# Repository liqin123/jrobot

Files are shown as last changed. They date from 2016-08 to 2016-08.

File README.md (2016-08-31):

jrobot
A PLEN Robot Derivative designed at China . We love the PLEN2 robot but its expensive. This is our take on a lower cost version of the PLEN2 robot using 9g servo's.

The 3d printed parts are inspired by the PLEN2 parts but were redrawn from scratch to make use of the cheaper 9g servo motors.

Note: This is a work in progress. We are still busy building and testing it. Proceed at own risk :)

Please get start kits [taobao $120](https://item.taobao.com/item.htm?spm=a230r.1.14.28.0Gwvvy&id=531972040644&ns=1&abbucket=7#detail)

qq group: 371582470
app: jrobot

video demo:http://v.youku.com/v_show/id_XMTcwMTE4NjE5Mg==.html?from=y1.7-2

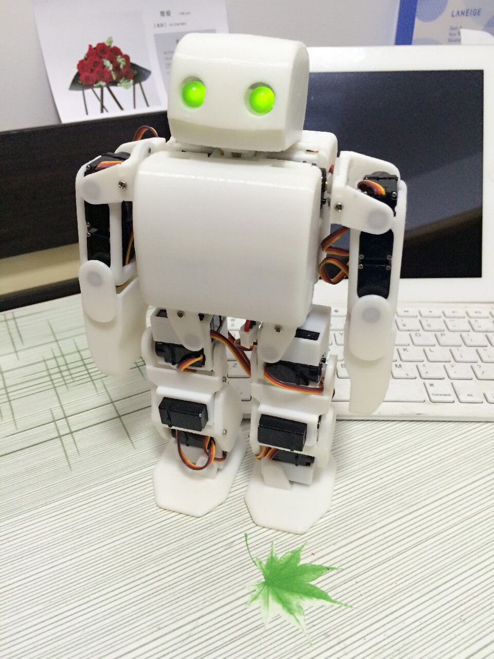
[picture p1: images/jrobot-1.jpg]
3d printed jrobot


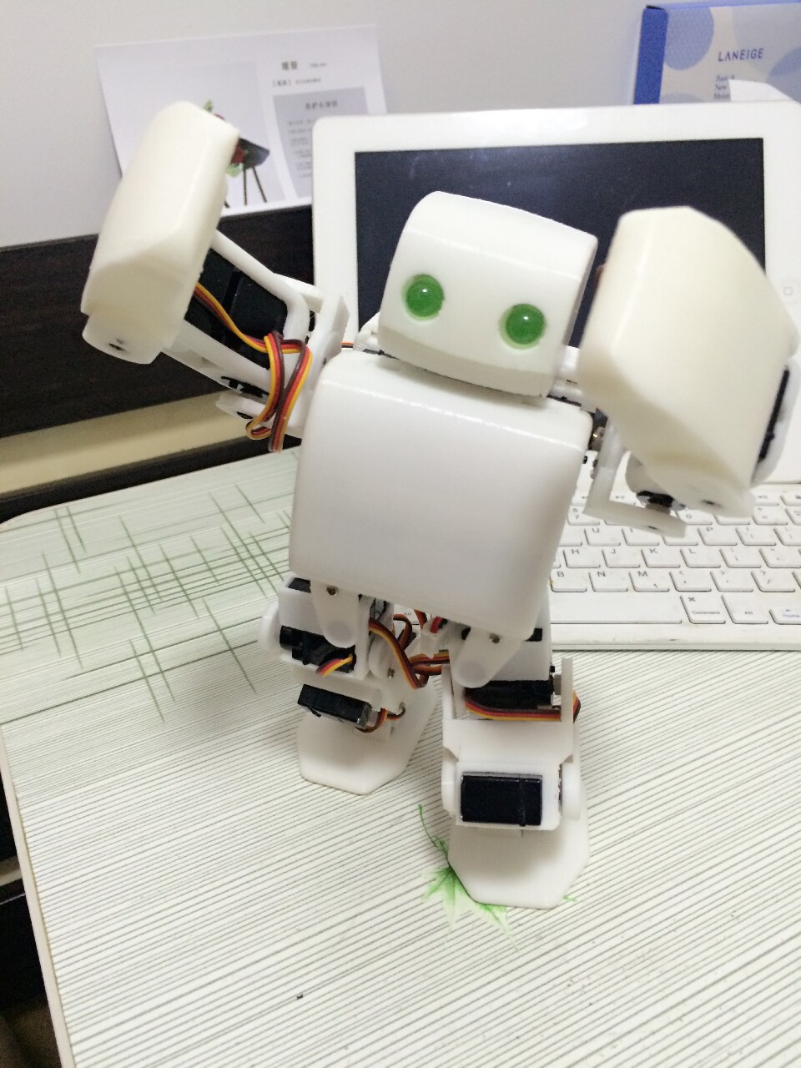
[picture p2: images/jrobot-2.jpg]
3d printed jrobot


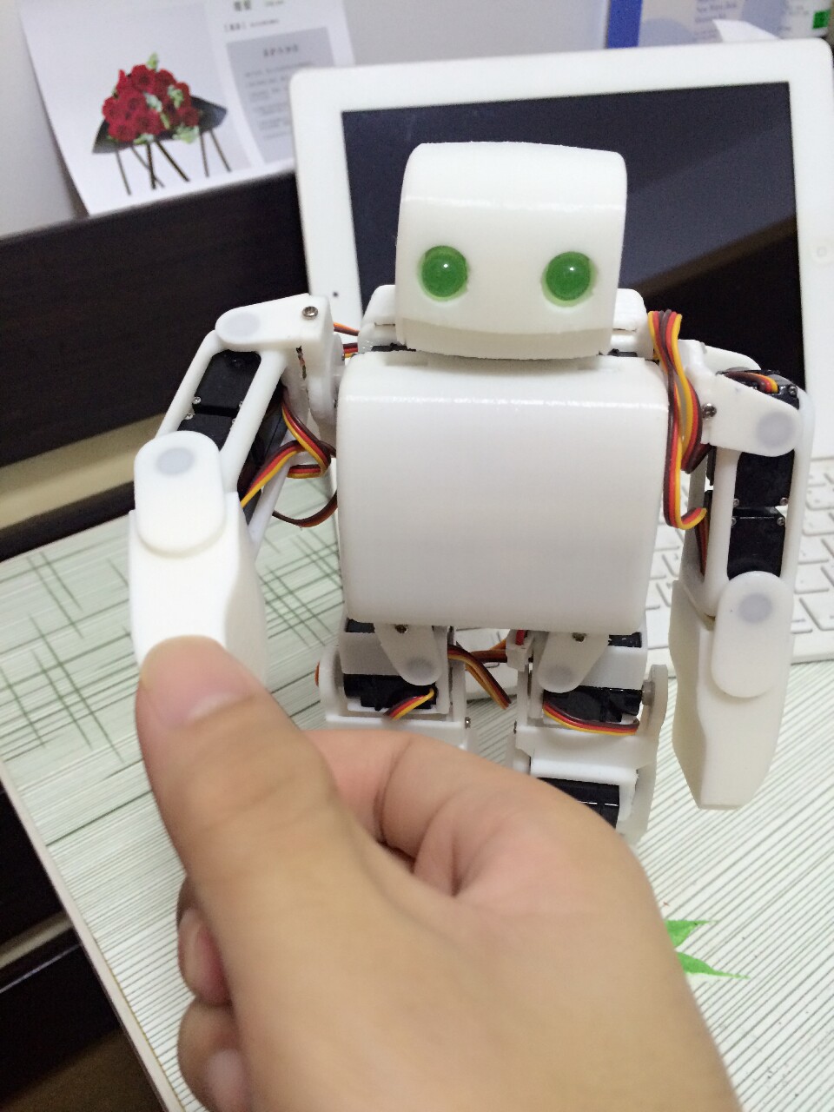
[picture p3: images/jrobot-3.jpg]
3d printed jrobot


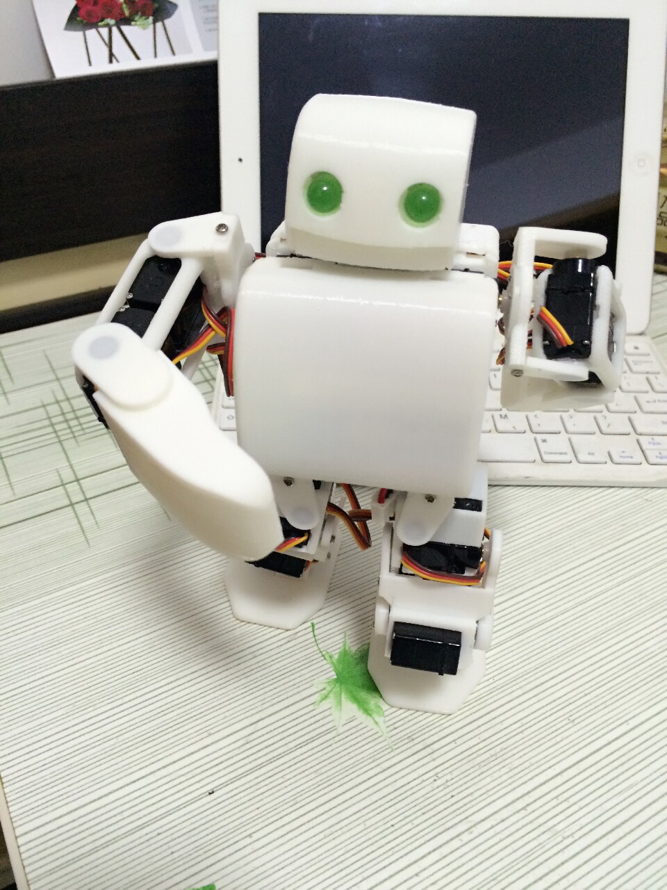
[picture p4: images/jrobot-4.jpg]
3d printed jrobot


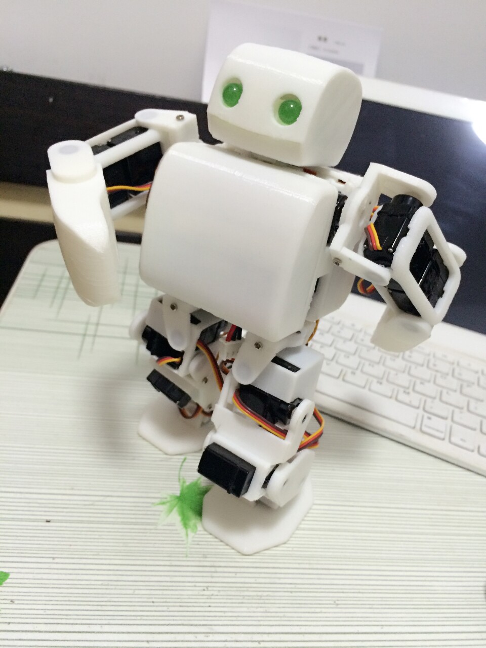
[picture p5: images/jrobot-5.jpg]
3d printed jrobot


This software is released under the MIT License.

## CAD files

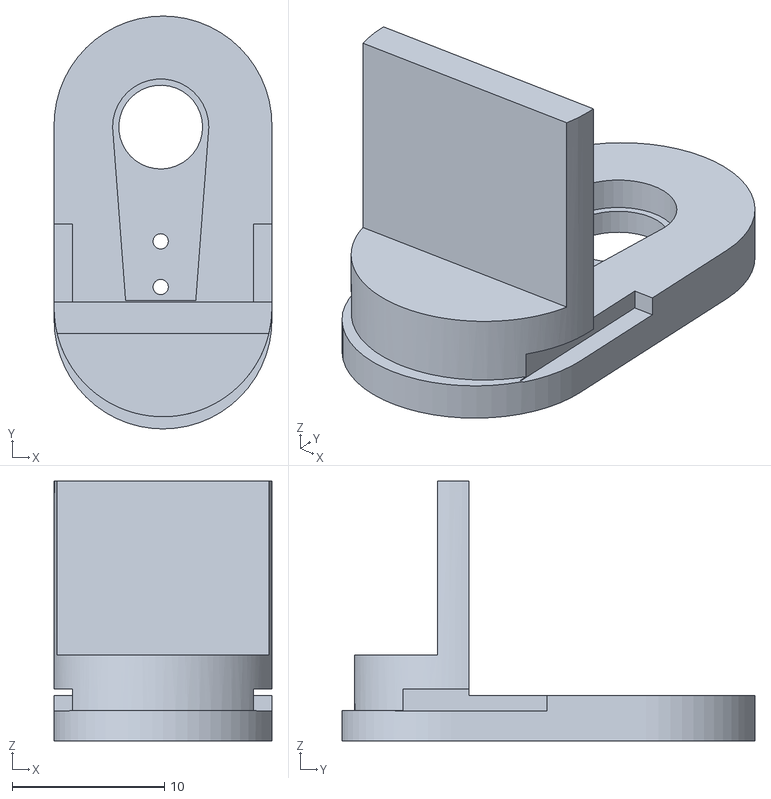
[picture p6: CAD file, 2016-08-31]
stl/servo_bracket_elbow_1.STL
14.3 x 27.1 x 17.1

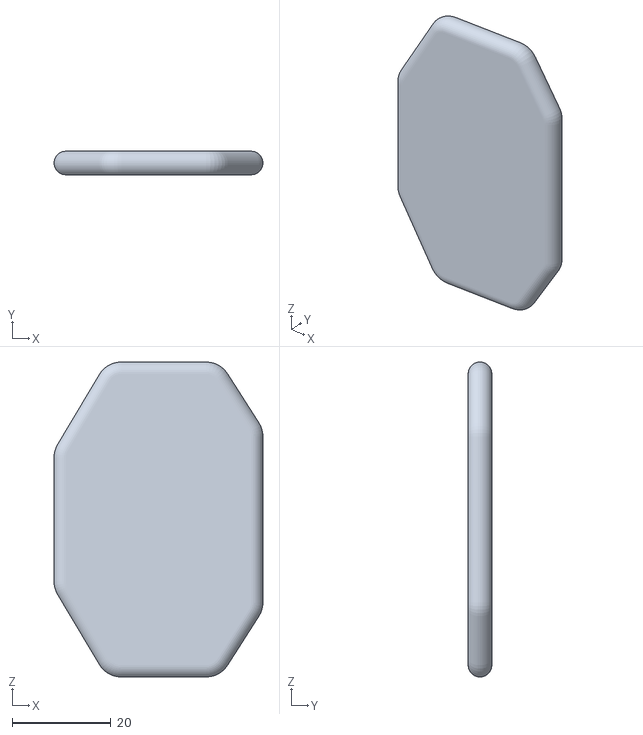
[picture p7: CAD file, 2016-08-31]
stl/foot.STL
42.4 x 4.80 x 63.9

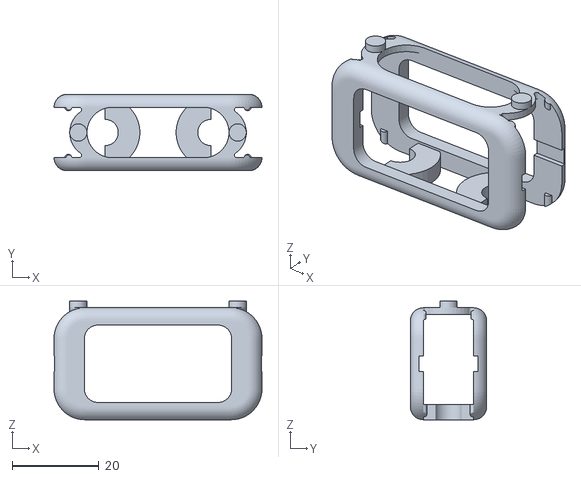
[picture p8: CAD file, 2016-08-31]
stl/servo_assem_type1.STL
47.9 x 17.6 x 27.3

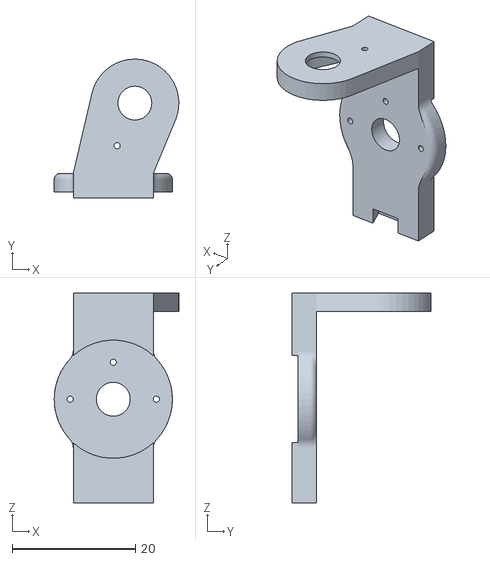
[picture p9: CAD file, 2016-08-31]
stl/servo_type_part2_mirror.STL
20.2 x 22.5 x 34.1

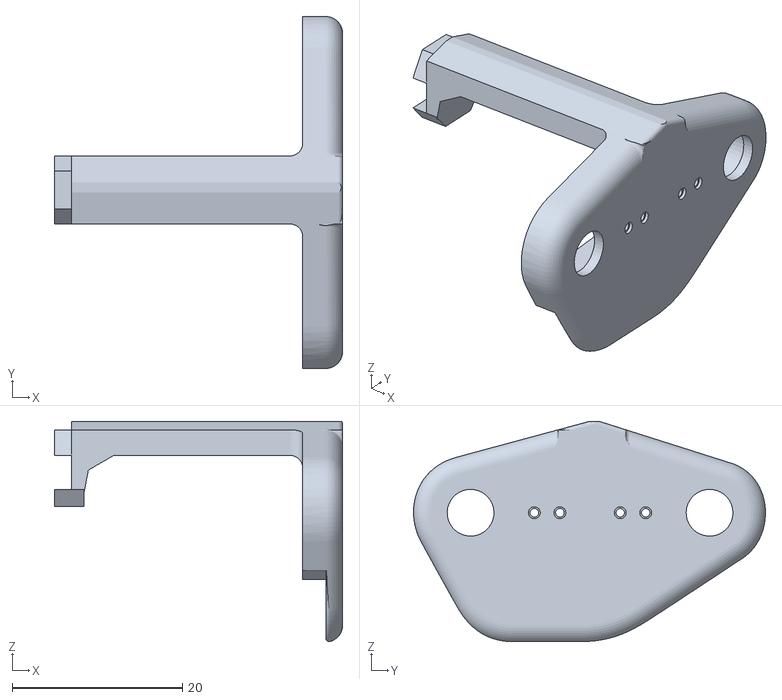
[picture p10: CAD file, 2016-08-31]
stl/servo_bracket_shin_part1.STL
33.9 x 41.4 x 25.9

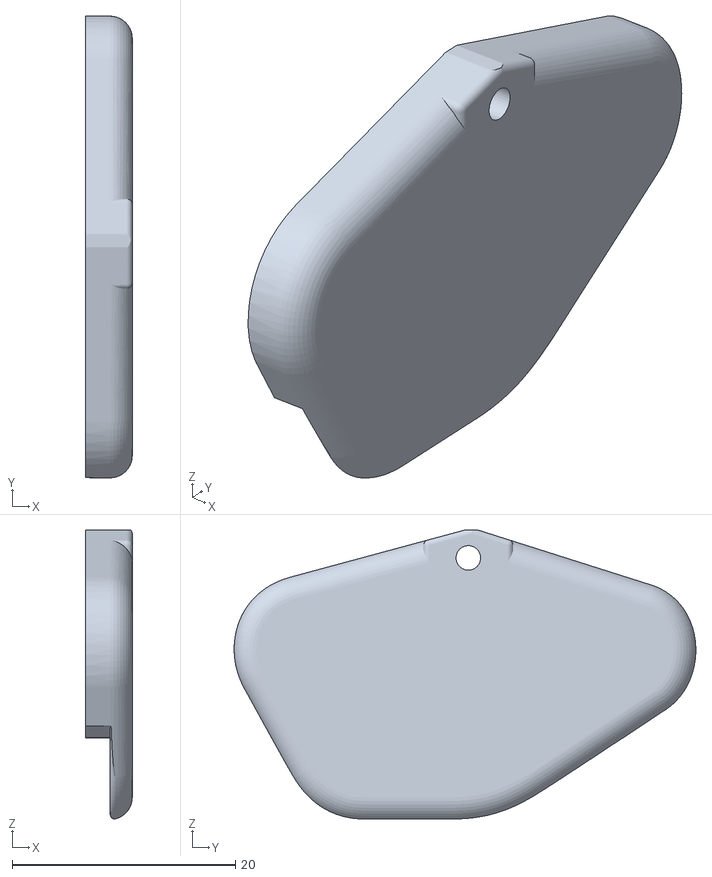
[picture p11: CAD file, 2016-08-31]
stl/servo_bracket_shin_part2.STL
4.18 x 41.4 x 25.9

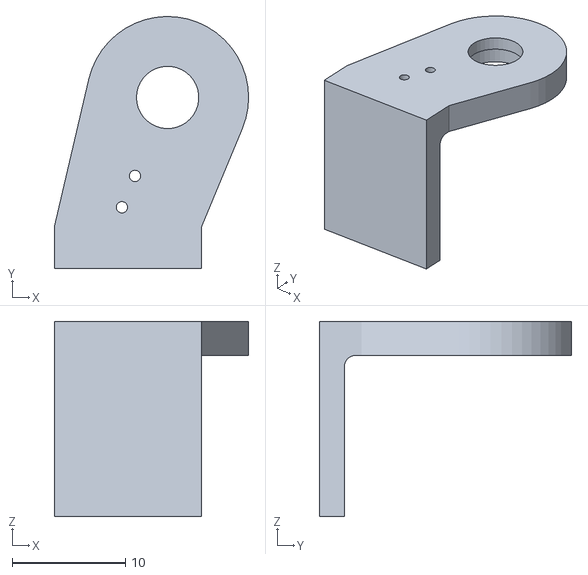
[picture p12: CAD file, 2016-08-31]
stl/servo_bracket_ankle_1_mirror.STL
17.2 x 22.2 x 17.2

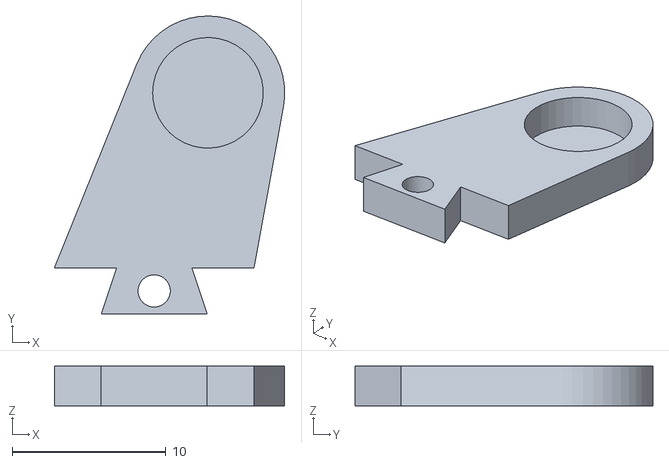
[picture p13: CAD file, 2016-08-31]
stl/servo_type_part1_mirror.STL
15.0 x 19.4 x 2.60

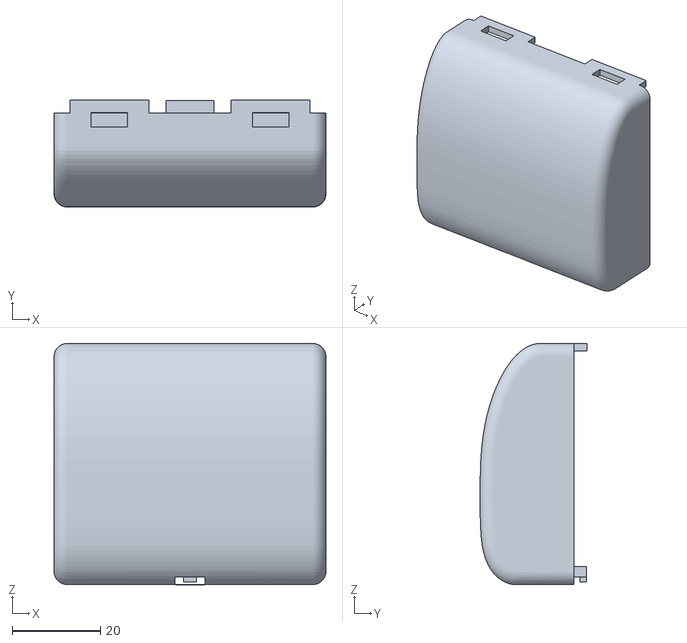
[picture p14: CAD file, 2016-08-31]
stl/body_front.STL
61.6 x 24.2 x 54.6

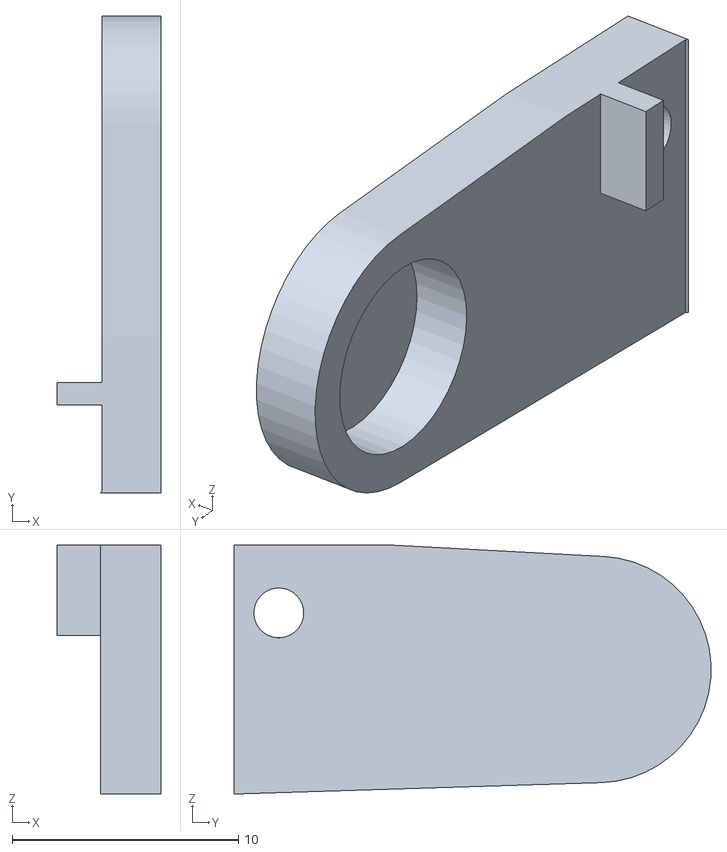
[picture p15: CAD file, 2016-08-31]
stl/servo_bracket_knee_part1_mirror.STL
4.60 x 21.1 x 11.0

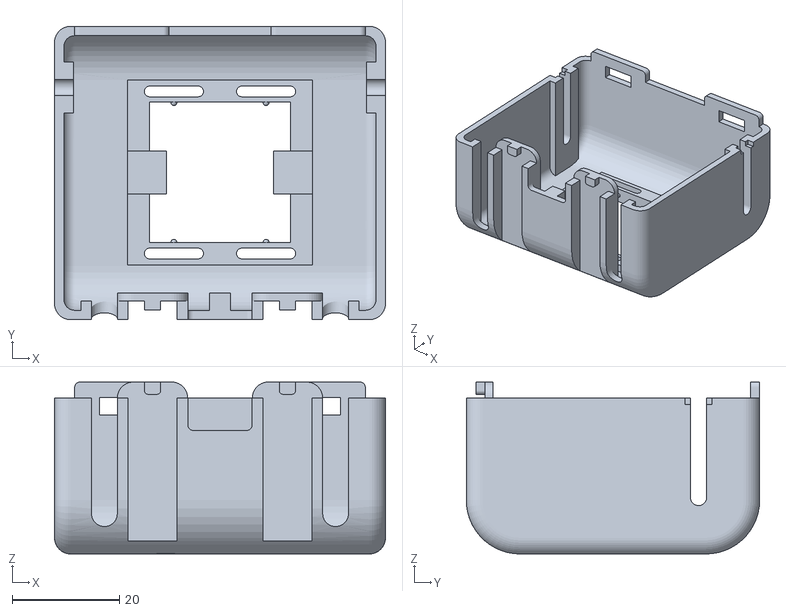
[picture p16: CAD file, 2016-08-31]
stl/body_rear.STL
61.6 x 54.6 x 32.0

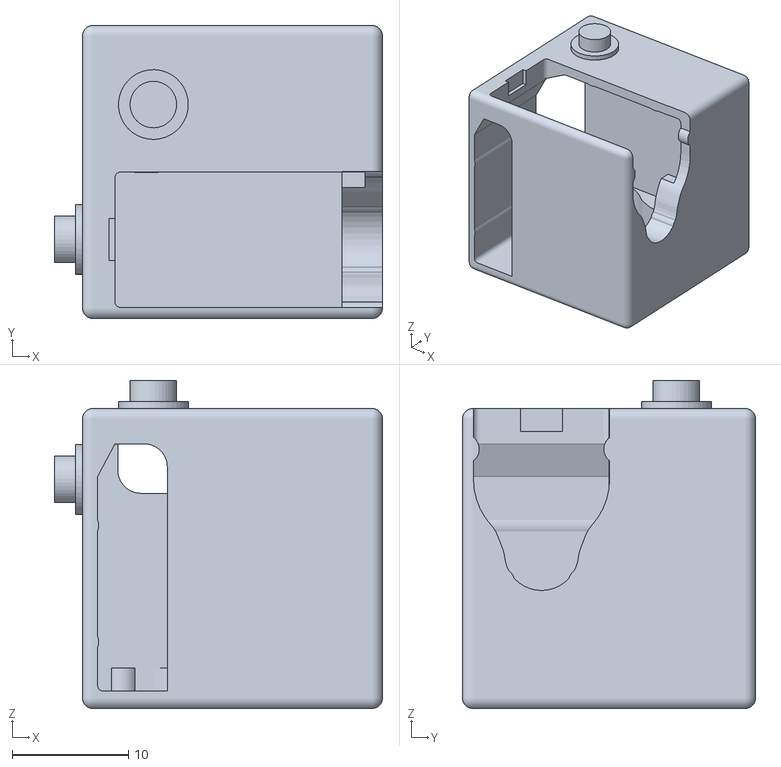
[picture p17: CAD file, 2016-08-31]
stl/servo_assem_type2_mirror.STL
28.2 x 25.2 x 28.2

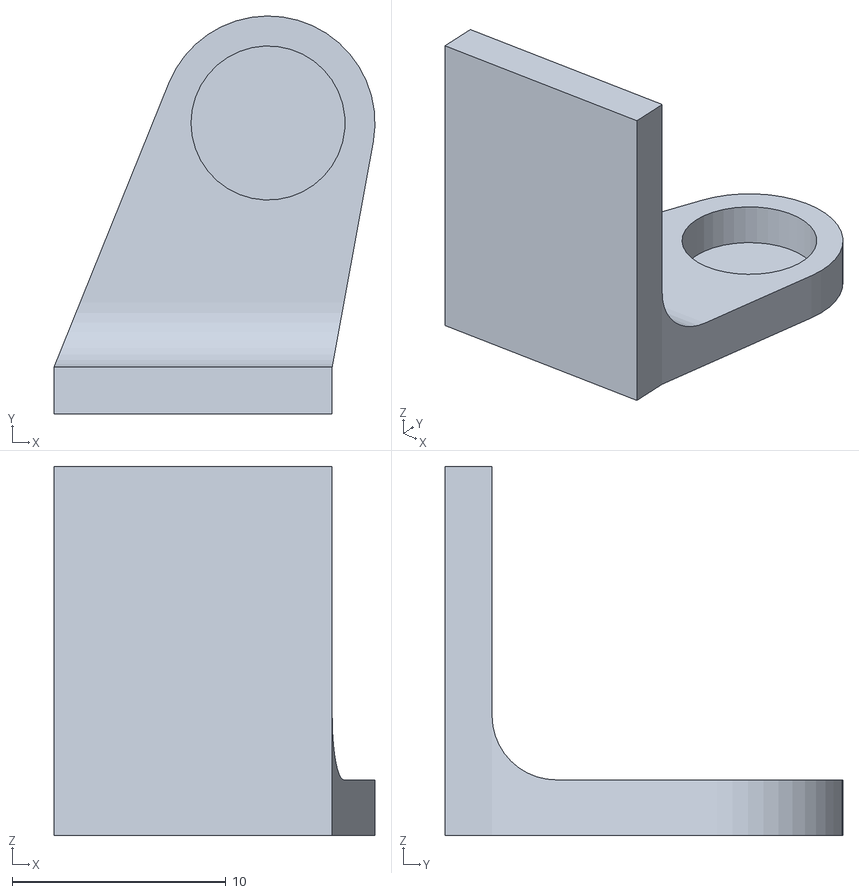
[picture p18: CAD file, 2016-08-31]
stl/servo_bracket_ankle_2_mirror.STL
15.0 x 18.6 x 17.2

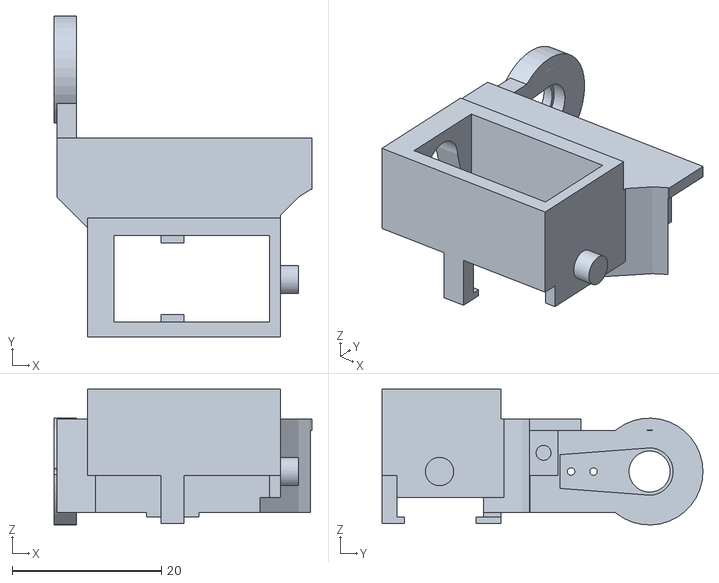
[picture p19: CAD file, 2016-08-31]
stl/servo_bracket_knee_part2_mirror.STL
34.5 x 42.9 x 18.2

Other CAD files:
stl/servo_type_part2.STL
stl/servo_bracket_ankle_1.STL
stl/servo_bracket_shin_part1_mirror.STL
stl/servo_bracket_shin_part2_mirror.STL
stl/barb.STL
stl/body_middle.STL
stl/foot_mirror.STL
stl/servo_assem_type2.STL
stl/servo_bracket_ankle_2.STL
stl/servo_bracket_elbow_2.STL
stl/servo_bracket_knee_part1.STL
stl/servo_bracket_knee_part2.STL
stl/servo_type_part1.STL

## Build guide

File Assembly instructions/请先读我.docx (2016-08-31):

1. 注意点：
  a) 关于电池：出厂锂电处于不饱和状态(不知道有多少电)，请先给电池充满电(充电器灯的状态会从红色->橙色->绿色，绿色时表示电池已经完全充满)
  b) 关于app：可以在IOS 应用市场或在Android二个应用市场 (应用宝 | 豌豆荚) 搜索jrobot 下载。请阅读app左侧菜单栏的帮助和反馈，了解如何配置网络和连接机器人。
  c) 关于app中的网络配置：请在配置前先关闭Robot电源，然后再SSID和密码端填入家里使用的路由器的SSID和密码(务必确保这两项正确，否则配置会失败)，然后打开Robot电源，此时要立刻点击APP中的配置按钮(超过30秒后，Robot会退出接受网络配置状态，进入创建自主热点模式，适合在无网络的地方使用)。若Robot进入了热点模式，可以使用手机在Wifi界面搜索Robot的热点一般名为Jrobot*****的热点，密码为12345678，接着就可以用APP控制Robot了。
  d) 关于舵机回中，PLEN2的仿人形结构和舵机的转动角度范围(<180度)限制每个舵机的初始角度不能是90度，而且每个关节的初始角度不一定一样，切记切记！！！

所以在安装关节的时候，请务必如下操作：

1.关闭主板电源

2.先把舵机插到主板上对应这个关节的舵机插槽

3.打开主板电源，舵机自动转到对应关节的初始位置。

4.关闭主板电源，安装关节。

5.打开主板电源，连上APP，在APP中的开发者模式->回中，将对应的关节微调，调正，然后点回中界面左侧的回中将调整后的回中角度保存到Robot

e) 关于舵机摆臂和轴承的处理：

1.轴承用于虚轴处，固定在打印件上，塞进去后，压平即可。

2.舵机摆臂用到了2中，一种是半一字的摆臂，用在腿各个关节和手关节，只 需要将摆臂末端稍微剪短后放入打印件用胶水固定(也可以关节安装完后再用胶水稍微固定下，前者刚性好，难安装，后者好安装，刚性略差);另外一种摆臂是圆形，用在肩关节和大腿根关节，用胶水固定后，重物压着，牢固后即可以安装。

2. 接线图：

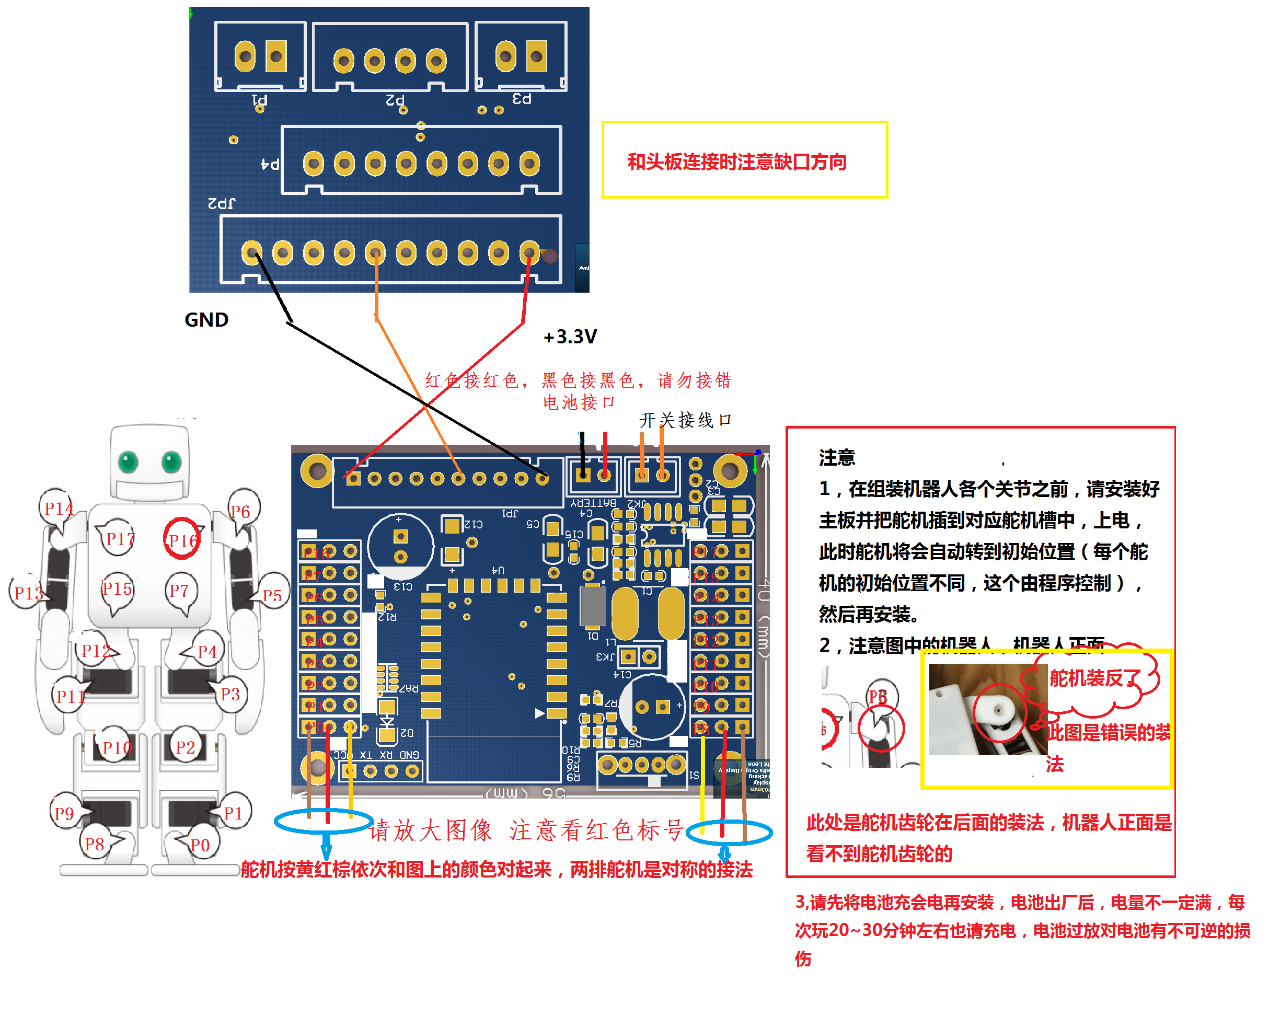
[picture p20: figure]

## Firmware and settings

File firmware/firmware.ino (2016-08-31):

 /*
	Copyright (c) 2015,
	- Kazuyuki TAKASE - https://github.com/junbowu
	- PLEN Project Company Inc. - https://plen.jp

	This software is released under the MIT License.
	(See also : http://opensource.org/licenses/mit-license.php)
*/

#include <string.h>

#include <Wire.h>
#include <Servo.h>

#include "JointController.h"
#include "Motion.h"
#include "MotionController.h"
#include "Interpreter.h"
#include "Pin.h"
#include "Parser.h"
#include "Protocol.h"
#include "System.h"
#include "Profiler.h"
#include "ExternalFs.h"

#if ENSOUL_PLEN2
	#include "AccelerationGyroSensor.h"
	#include "Soul.h"
#endif

namespace
{
	using namespace PLEN2;

	/*!
		Core instances
	*/
	JointController  joint_ctrl;
	MotionController motion_ctrl(joint_ctrl);
	Interpreter      interpreter(motion_ctrl);

	#if ENSOUL_PLEN2
		AccelerationGyroSensor sensor;
		Soul                   soul(sensor, motion_ctrl);
	#endif

	/*!
		The application instance
	*/
	class Application : public Protocol
	{
	private:
		static void (Application::*CONTROLLER_EVENT_HANDLER[])();
		static void (Application::*INTERPRETER_EVENT_HANDLER[])();
		static void (Application::*SETTER_EVENT_HANDLER[])();
		static void (Application::*GETTER_EVENT_HANDLER[])();

		static void (Application::**EVENT_HANDLER[])();

		Motion::Header    m_header_tmp;
		Motion::Frame     m_frame_tmp;
		Interpreter::Code m_code_tmp;

		void applyDiff()
		{
			#if DEBUG_LESS
				volatile Utility::Profiler p(F("Application::applyDiff()"));

				System::debugSerial().print(F(">>> joint_id : "));
				System::debugSerial().println(Utility::hexbytes2uint(m_buffer.data, 2));

				System::debugSerial().print(F(">>> angle_diff : "));
				System::debugSerial().println(Utility::hexbytes2int(m_buffer.data + 2, 3));
			#endif

			joint_ctrl.setAngleDiff(
				Utility::hexbytes2uint(m_buffer.data, 2),
				Utility::hexbytes2int(m_buffer.data + 2, 3)
			);
		}

		void apply()
		{
			#if DEBUG_LESS
				volatile Utility::Profiler p(F("Application::apply()"));
            
				System::debugSerial().print(F(">>> joint_id : "));
				System::debugSerial().println(Utility::hexbytes2uint(m_buffer.data, 2));

				System::debugSerial().print(F(">>> angle : "));
				System::debugSerial().println(Utility::hexbytes2int(m_buffer.data + 2, 3));
			#endif

			joint_ctrl.setAngle(
				Utility::hexbytes2uint(m_buffer.data, 2),
				Utility::hexbytes2int(m_buffer.data + 2, 3)
			);
		}

		void homePosition()
		{
			#if DEBUG_LESS
				volatile Utility::Profiler p(F("Application::homePosition()"));
			#endif

			joint_ctrl.loadSettings();
		}

		void playMotion()
		{
			#if DEBUG_LESS
				volatile Utility::Profiler p(F("Application::playMotion()"));

				System::debugSerial().print(F(">>> slot : "));
				System::debugSerial().println(Utility::hexbytes2uint(m_buffer.data, 2));
			#endif

			motion_ctrl.play(
				Utility::hexbytes2uint(m_buffer.data, 2)
			);
		}

		void stopMotion()
		{
			#if DEBUG_LESS
				volatile Utility::Profiler p(F("Application::stopMotion()"));
			#endif

			motion_ctrl.willStop();
		}

		void popCode()
		{
			#if DEBUG_LESS
				volatile Utility::Profiler p(F("Application::popCode()"));
			#endif

			interpreter.popCode();
		}

		void pushCode()
		{
			#if DEBUG_LESS
				volatile Utility::Profiler p(F("Application::pushCode()"));

				System::debugSerial().print(F(">>> slot : "));
				System::debugSerial().println(Utility::hexbytes2uint(m_buffer.data, 2));

				System::debugSerial().print(F(">>> loop_count : "));
				System::debugSerial().println(Utility::hexbytes2uint(m_buffer.data + 2, 2));
			#endif

			m_code_tmp.slot       = Utility::hexbytes2uint(m_buffer.data, 2);
			m_code_tmp.loop_count = Utility::hexbytes2uint(m_buffer.data + 2, 2) - 1;

			interpreter.pushCode(m_code_tmp);
		}

		void resetInterpreter()
		{
			#if DEBUG_LESS
				volatile Utility::Profiler p(F("Application::resetInterpreter()"));
			#endif

			interpreter.reset();
		}

		void setHome()
		{
			#if DEBUG_LESS
				volatile Utility::Profiler p(F("Application::setHome()"));

				System::debugSerial().print(F(">>> joint_id : "));
				System::debugSerial().println(Utility::hexbytes2uint(m_buffer.data, 2));

				System::debugSerial().print(F(">>> angle : "));
				System::debugSerial().println(Utility::hexbytes2int(m_buffer.data + 2, 3));
			#endif

			joint_ctrl.setHomeAngle(
				Utility::hexbytes2uint(m_buffer.data, 2),
				Utility::hexbytes2int(m_buffer.data + 2, 3)
			);
		}

		void setJointSettings()
		{
			#if DEBUG_LESS
				volatile Utility::Profiler p(F("Application::setJointSettings()"));
			#endif

			joint_ctrl.resetSettings();
		}

		void setMax()
		{
			#if DEBUG_LESS
				volatile Utility::Profiler p(F("Application::setMax()"));

				System::debugSerial().print(F(">>> joint_id : "));
				System::debugSerial().println(Utility::hexbytes2uint(m_buffer.data, 2));

				System::debugSerial().print(F(">>> angle : "));
				System::debugSerial().println(Utility::hexbytes2int(m_buffer.data + 2, 3));
			#endif

			joint_ctrl.setMaxAngle(
				Utility::hexbytes2uint(m_buffer.data, 2),
				Utility::hexbytes2int(m_buffer.data + 2, 3)
			);
		}

		void setMotionFrame()
		{
			#if DEBUG_LESS
				volatile Utility::Profiler p(F("Application::setMotionFrame()"));

				System::debugSerial().print(F(">>> slot : "));
				System::debugSerial().println(Utility::hexbytes2uint(m_buffer.data, 2));

				System::debugSerial().print(F(">>> frame_id : "));
				System::debugSerial().println(Utility::hexbytes2uint(m_buffer.data + 2, 2));

				System::debugSerial().print(F(">>> transition_time_ms : "));
				System::debugSerial().println(Utility::hexbytes2uint(m_buffer.data + 4, 4));

				for (int device_id = 0; device_id < JointController::SUM; device_id++)
				{
					System::debugSerial().print(F(">>> output["));
					System::debugSerial().print(device_id);
					System::debugSerial().print(F("] : "));
					System::debugSerial().println(Utility::hexbytes2int(m_buffer.data + 8 + device_id * 4, 4));
				}
			#endif

			m_frame_tmp.transition_time_ms = Utility::hexbytes2uint(m_buffer.data + 4, 4);

			for (char device_id = 0; device_id < JointController::SUM; device_id++)
			{
				m_frame_tmp.joint_angle[device_id] = Utility::hexbytes2int(m_buffer.data + 8 + device_id * 4, 4);
			}

			if (m_installing)
			{
				if (m_frame_tmp.index < m_header_tmp.frame_length)
				{
					m_frame_tmp.set(m_header_tmp.slot);
					m_frame_tmp.index++;
				}

				if (m_frame_tmp.index == m_header_tmp.frame_length)
				{
					m_installing = false;
				}
				else
				{
					readByte('>');
					accept();
					transitState();

					readByte('m');
					readByte('f');
					accept();
					transitState();

					readByte('0'); // dummy
					readByte('0'); // dummy
					readByte('0'); // dummy
					readByte('0'); // dummy
				}
			}
			else
			{
				m_frame_tmp.index = Utility::hexbytes2uint(m_buffer.data + 2, 2);
				m_frame_tmp.set(Utility::hexbytes2uint(m_buffer.data, 2));
			}
		}

		void setMotionHeader()
		{
			strncpy(m_header_tmp.name, m_buffer.data + 2, 20);
			m_header_tmp.name[20] = '\0';
			m_buffer.data[2]      = '\0';

			if (   !(m_parser[ARGUMENTS_INCOMING]->parse(m_buffer.data))
				|| !(m_parser[ARGUMENTS_INCOMING]->parse(m_buffer.data + 22)) )
			{
				return;
			}

			#if DEBUG_LESS
				volatile Utility::Profiler p(F("Application::setMotionHeader()"));

				System::debugSerial().print(F(">>> slot : "));
				System::debugSerial().println(Utility::hexbytes2uint(m_buffer.data, 2));

				System::debugSerial().print(F(">>> name : "));
				System::debugSerial().println(m_header_tmp.name);

				System::debugSerial().print(F(">>> func : "));
				System::debugSerial().println(Utility::hexbytes2uint(m_buffer.data + 22, 2));

				System::debugSerial().print(F(">>> arg0 : "));
				System::debugSerial().println(Utility::hexbytes2uint(m_buffer.data + 24, 2));

				System::debugSerial().print(F(">>> arg1 : "));
				System::debugSerial().println(Utility::hexbytes2uint(m_buffer.data + 26, 2));

				System::debugSerial().print(F(">>> frame_length : "));
				System::debugSerial().println(Utility::hexbytes2uint(m_buffer.data + 28, 2));
			#endif

			m_header_tmp.slot         = Utility::hexbytes2uint(m_buffer.data, 2);
			m_header_tmp.frame_length = Utility::hexbytes2uint(m_buffer.data + 28, 2);

			switch (Utility::hexbytes2uint(m_buffer.data + 22, 2))
			{
				case 0:
				{
					m_header_tmp.use_loop = 0;
					m_header_tmp.use_jump = 0;

					break;
				}

				case 1:
				{
					m_header_tmp.use_loop   = 1;
					m_header_tmp.use_jump   = 0;
					m_header_tmp.loop_begin = Utility::hexbytes2uint(m_buffer.data + 24, 2);
					m_header_tmp.loop_end   = Utility::hexbytes2uint(m_buffer.data + 26, 2);

					break;
				}

				case 2:
				{
					m_header_tmp.use_loop  = 0;
					m_header_tmp.use_jump  = 1;
					m_header_tmp.jump_slot = Utility::hexbytes2uint(m_buffer.data + 24, 2);

					break;
				}
			}

			m_header_tmp.set();

			if (m_installing == true)
			{
				readByte('>');
				accept();
				transitState();

				readByte('m');
				readByte('f');
				accept();
				transitState();

				readByte('0'); // dummy
				readByte('0'); // dummy
				readByte('0'); // dummy
				readByte('0'); // dummy

				m_frame_tmp.index = 0;
			}
		}

		void setMin()
		{
			#if DEBUG_LESS
				volatile Utility::Profiler p(F("Application::setMin()"));

				System::debugSerial().print(F(">>> joint_id : "));
				System::debugSerial().println(Utility::hexbytes2uint(m_buffer.data, 2));

				System::debugSerial().print(F(">>> angle : "));
				System::debugSerial().println(Utility::hexbytes2int(m_buffer.data + 2, 3));
			#endif

			joint_ctrl.setMinAngle(
				Utility::hexbytes2uint(m_buffer.data, 2),
				Utility::hexbytes2int(m_buffer.data + 2, 3)
			);
		}

		void getJointSettings()
		{
			#if DEBUG_LESS
				volatile Utility::Profiler p(F("Application::getJointSettings()"));
			#endif

			joint_ctrl.dump();
		}

		void getMotion()
		{
			#if DEBUG_LESS
				volatile Utility::Profiler p(F("Application::getMotion()"));

				System::debugSerial().print(F(">>> slot : "));
				System::debugSerial().println(Utility::hexbytes2uint(m_buffer.data, 2));
			#endif

			motion_ctrl.dump(
				Utility::hexbytes2uint(m_buffer.data, 2)
			);
		}

		void getVersionInformation()
		{
			#if DEBUG_LESS
				volatile Utility::Profiler p(F("Application::getVersionInformation()"));
			#endif

			System::dump();
		}

	public:
		virtual void afterHook()
		{
			#if DEBUG
				volatile Utility::Profiler p(F("Application::afterFook()"));
			#endif

			if (m_state == HEADER_INCOMING)
			{
				unsigned char header_id = m_parser[HEADER_INCOMING ]->index();
				unsigned char cmd_id    = m_parser[COMMAND_INCOMING]->index();

				(this->*EVENT_HANDLER[header_id][cmd_id])();

				#if ENSOUL_PLEN2
					soul.userActionInputed();
				#endif
			}
		}
	};

	void (Application::*Application::CONTROLLER_EVENT_HANDLER[])() = {
		&Application::applyDiff,
		&Application::apply,
		&Application::homePosition,
		&Application::playMotion,
		&Application::stopMotion,
		&Application::playMotion,
		&Application::stopMotion
	};

	void (Application::*Application::INTERPRETER_EVENT_HANDLER[])() = {
		&Application::popCode,
		&Application::pushCode,
		&Application::resetInterpreter
	};

	void (Application::*Application::SETTER_EVENT_HANDLER[])() = {
		&Application::setHome,
		&Application::setMotionHeader, // sanity check.
		&Application::setJointSettings,
		&Application::setMax,
		&Application::setMotionFrame,
		&Application::setMotionHeader,
		&Application::setMin
	};

	void (Application::*Application::GETTER_EVENT_HANDLER[])() = {
		&Application::getJointSettings,
		&Application::getMotion,
		&Application::getVersionInformation
	};

	void (Application::**Application::EVENT_HANDLER[])() = {
		Application::CONTROLLER_EVENT_HANDLER,
		Application::INTERPRETER_EVENT_HANDLER,
		Application::SETTER_EVENT_HANDLER,
		Application::GETTER_EVENT_HANDLER
	};

	Application app;
}


/*!
	@brief Setup

	Put your setup code here, to run once:

	@attention
	Digital pin's output is an indefinite if you don't give an initialize value.
	Please ensure that setup the pins which are configurable.
*/
void setup()
{
	volatile PLEN2::System system;
	ExternalFs::init();

	joint_ctrl.Init();
	joint_ctrl.loadSettings();
	System::setup_smartconfig();

	#if ENSOUL_PLEN2
		/*!
			@attention
			The order of power supplied or firmware startup timing is base-board, head-board.
			If the sampling method calls from early timing, program freezes because synchronism of communication is missed.
			(Generally, it is going to success setup() inserts 3000[msec] delays.)
		*/
		delay(3000);
	#endif

	#if DEBUG
		while (!Serial);

		PLEN2::System::outputSerial().println(
			F("Hello, I am PLEN2! My system is up and running ver.1.3.1, Let me walk :)")
		);
	#endif
}


/*!
	@brief Main polling loop

	Put your main code here, to run repeatedly:
*/
void loop()
{
	if (motion_ctrl.playing())
	{
		if (motion_ctrl.frameUpdatable())
		{
			motion_ctrl.updateFrame();
		}

		if (motion_ctrl.updatingFinished())
		{
			if (motion_ctrl.nextFrameLoadable())
			{
				motion_ctrl.loadNextFrame();
			}
			else
			{
				motion_ctrl.stop();

				if (interpreter.ready())
				{
					interpreter.popCode();
				}
			}
		}
	}

	if (PLEN2::System::SystemSerial().available())
	{
		app.readByte(PLEN2::System::SystemSerial().read());

		if (app.accept())
		{
			app.transitState();

		}
	}
	if (PLEN2::System::tcp_available())
	{
	#if DEBUG_LESS
	    uint8_t c = PLEN2::System::tcp_read();
     	    PLEN2::System::outputSerial().write(c);
     	    app.readByte(c);
        #else
            app.readByte(PLEN2::System::tcp_read());
        #endif
	    if (app.accept())
	    {
	        app.transitState();
	    }
	}

	PLEN2::System::handleClient();
	#if ENSOUL_PLEN2
		soul.log();
		soul.action();
	#endif
}

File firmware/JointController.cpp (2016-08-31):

/*
	Copyright (c) 2015,
	- Kazuyuki TAKASE - https://github.com/junbowu
	- PLEN Project Company Inc. - https://plen.jp

	This software is released under the MIT License.
	(See also : http://opensource.org/licenses/mit-license.php)
*/
#include "Arduino.h"
#include <Wire.h>
#include <Servo.h>
#include <Ticker.h>
#include <Adafruit_PWMServoDriver.h>

#include "Pin.h"
#include "Profiler.h"
#include "System.h"
#include "JointController.h"
#include "ExternalFs.h"
#include "Motion.h"

Adafruit_PWMServoDriver pwm;
Servo GPIO12SERVO;
Servo GPIO14SERVO;
Servo EyeOut;
Ticker flipper;
Ticker flipper_second;

extern File fp_config;
/*!
	@note
	If you want to apply the firmware to PLEN1.4, set the macro to false.
*/
#define PLEN2_JOINTCONTROLLER_PWM_OUT_00_07_REGISTER OCR1C
#define PLEN2_JOINTCONTROLLER_PWM_OUT_08_15_REGISTER OCR1B
#define PLEN2_JOINTCONTROLLER_PWM_OUT_16_23_REGISTER OCR1A

volatile bool PLEN2::JointController::m_1cycle_finished = false;
int PLEN2::JointController::m_pwms[PLEN2::JointController::SUM];

//eyes control
int _enable;
int _eye_count_step;
int _eye_count;

namespace
{
	namespace Shared
	{
		using namespace PLEN2;

		PROGMEM const int m_SETTINGS_INITIAL[] =
		{
			JointController::ANGLE_MIN, JointController::ANGLE_MAX,  -40, // [01] Left : Shoulder Pitch
			JointController::ANGLE_MIN, JointController::ANGLE_MAX,  245, // [02] Left : Thigh Yaw
			JointController::ANGLE_MIN, JointController::ANGLE_MAX,  470, // [03] Left : Shoulder Roll
			JointController::ANGLE_MIN, JointController::ANGLE_MAX, -100, // [04] Left : Elbow Roll
			JointController::ANGLE_MIN, JointController::ANGLE_MAX, -205, // [05] Left : Thigh Roll
			JointController::ANGLE_MIN, JointController::ANGLE_MAX,   50, // [06] Left : Thigh Pitch
			JointController::ANGLE_MIN, JointController::ANGLE_MAX,  445, // [07] Left : Knee Pitch
			JointController::ANGLE_MIN, JointController::ANGLE_MAX,  245, // [08] Left : Foot Pitch
			JointController::ANGLE_MIN, JointController::ANGLE_MAX,  -75, // [09] Left : Foot Roll
			JointController::ANGLE_MIN, JointController::ANGLE_MAX, JointController::ANGLE_NEUTRAL,
			JointController::ANGLE_MIN, JointController::ANGLE_MAX, JointController::ANGLE_NEUTRAL,
			JointController::ANGLE_MIN, JointController::ANGLE_MAX, JointController::ANGLE_NEUTRAL,
			JointController::ANGLE_MIN, JointController::ANGLE_MAX,   15, // [10] Right : Shoulder Pitch
			JointController::ANGLE_MIN, JointController::ANGLE_MAX,  -70, // [11] Right : Thigh Yaw
			JointController::ANGLE_MIN, JointController::ANGLE_MAX, -390, // [12] Right : Shoulder Roll
			JointController::ANGLE_MIN, JointController::ANGLE_MAX,  250, // [13] Right : Elbow Roll
			JointController::ANGLE_MIN, JointController::ANGLE_MAX,  195, // [14] Right : Thigh Roll
			JointController::ANGLE_MIN, JointController::ANGLE_MAX, -105, // [15] Right : Thigh Pitch
			JointController::ANGLE_MIN, JointController::ANGLE_MAX, -510, // [16] Right : Knee Pitch
			JointController::ANGLE_MIN, JointController::ANGLE_MAX, -305, // [17] Right : Foot Pitch
			JointController::ANGLE_MIN, JointController::ANGLE_MAX,   60, // [18] Right : Foot Roll
			JointController::ANGLE_MIN, JointController::ANGLE_MAX, JointController::ANGLE_NEUTRAL,
			JointController::ANGLE_MIN, JointController::ANGLE_MAX, JointController::ANGLE_NEUTRAL,
			JointController::ANGLE_MIN, JointController::ANGLE_MAX, JointController::ANGLE_NEUTRAL
		};

		const int ERROR_LVALUE = -32768;
	}
}


void PLEN2::JointController::Init()
{
	pwm = Adafruit_PWMServoDriver();

    pinMode(Pin::PCA9685_ENABLE(), OUTPUT);
    digitalWrite(Pin::PCA9685_ENABLE(), LOW);

    // Software PWM PIN
    GPIO12SERVO.attach(Pin::PWM_OUT_12());
    GPIO14SERVO.attach(Pin::PWM_OUT_14());

    _enable = false;
    _eye_count = 100;
    EyeOut.attach(Pin::LED_OUT(), 200, 15000);

    pinMode(Pin::PCA9685_ENABLE(), OUTPUT);
    digitalWrite(Pin::PCA9685_ENABLE(), LOW);

    // Initialize I2C
    Wire.begin(4, 5);

    // PWMServoDriver
    pwm.begin();
    pwm.setPWMFreq(PWM_FREQ());   // servos run at 300Hz updates

    delay(500);
    
	for (char joint_id = 0; joint_id < SUM; joint_id++)
	{
		m_SETTINGS[joint_id].MIN  = Shared::m_SETTINGS_INITIAL[joint_id * 3];
		m_SETTINGS[joint_id].MAX  = Shared::m_SETTINGS_INITIAL[joint_id * 3 + 1];
		m_SETTINGS[joint_id].HOME = Shared::m_SETTINGS_INITIAL[joint_id * 3 + 2];
		setAngle(joint_id, m_SETTINGS[joint_id].HOME);
	}
}
PLEN2::JointController::JointController()
{

}


void PLEN2::JointController::loadSettings()
{
	#if DEBUG
		volatile Utility::Profiler p(F("JointController::loadSettings()"));
	#endif

	unsigned char* filler = reinterpret_cast<unsigned char*>(m_SETTINGS);
	
	if (ExternalFs::readByte(INIT_FLAG_ADDRESS(), fp_config) != INIT_FLAG_VALUE())
	{
		ExternalFs::writeByte(INIT_FLAG_ADDRESS(), INIT_FLAG_VALUE(), fp_config);
        ExternalFs::write(SETTINGS_HEAD_ADDRESS(), sizeof(m_SETTINGS), filler, fp_config);
		System::debugSerial().println(F("reset config\n"));
	}
	else
	{
		ExternalFs::read(SETTINGS_HEAD_ADDRESS(), sizeof(m_SETTINGS), filler, fp_config);
		System::debugSerial().println(F("read config"));
	}

	for (char joint_id = 0; joint_id < SUM; joint_id++)
	{
		setAngle(joint_id, m_SETTINGS[joint_id].HOME);
	}

    flipper.attach_ms(Motion::Frame::UPDATE_INTERVAL_MS, PLEN2::JointController::updateAngle);
    flipper_second.attach(1, PLEN2::JointController::updateEyes);
}


void PLEN2::JointController::resetSettings()
{
	#if DEBUG
		volatile Utility::Profiler p(F("JointController::resetSettings()"));
	#endif
	
    ExternalFs::writeByte(INIT_FLAG_ADDRESS(), INIT_FLAG_VALUE(), fp_config);

	for (char joint_id = 0; joint_id < SUM; joint_id++)
	{
		m_SETTINGS[joint_id].MIN  = Shared::m_SETTINGS_INITIAL[joint_id * 3];
		m_SETTINGS[joint_id].MAX  = Shared::m_SETTINGS_INITIAL[joint_id * 3 + 1];
		m_SETTINGS[joint_id].HOME = Shared::m_SETTINGS_INITIAL[joint_id * 3 + 2];

		setAngle(joint_id, m_SETTINGS[joint_id].HOME);
	}
	
    ExternalFs::write(SETTINGS_HEAD_ADDRESS(), sizeof(m_SETTINGS), 
                    reinterpret_cast<const unsigned char*>(m_SETTINGS), fp_config);
}


const int& PLEN2::JointController::getMinAngle(unsigned char joint_id)
{
	#if DEBUG
		volatile Utility::Profiler p(F("JointController::getMinAngle()"));
	#endif

	if (joint_id >= SUM)
	{
		#if DEBUG
			System::debugSerial().print(F(">>> bad argment! : joint_id = "));
			System::debugSerial().println(static_cast<int>(joint_id));
		#endif

		return Shared::ERROR_LVALUE;
	}

	return m_SETTINGS[joint_id].MIN;
}


const int& PLEN2::JointController::getMaxAngle(unsigned char joint_id)
{
	#if DEBUG
		volatile Utility::Profiler p(F("JointController::getMaxAngle()"));
	#endif

	if (joint_id >= SUM)
	{
		#if DEBUG
			System::debugSerial().print(F(">>> bad argment! : joint_id = "));
			System::debugSerial().println(static_cast<int>(joint_id));
		#endif

		return Shared::ERROR_LVALUE;
	}

	return m_SETTINGS[joint_id].MAX;
}
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

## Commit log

2016-08-31 add jrobot stl
    [barb.STL, body_front.STL, body_middle.STL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]
2016-08-31 add assembly instruction
